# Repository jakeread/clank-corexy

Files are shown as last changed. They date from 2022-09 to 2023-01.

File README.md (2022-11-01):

## Clank-CoreXY

This is the CAD repo for the "minimal" variant of the [clank](https://clank.tools) machine platform: easily fabricated, multi-purpose cnc tools. Part of the [mtm project](mtm.cba.mit.edu) at the [MIT Center for Bits and Atoms](cba.mit.edu)

Read the [dev log](log/clank-corexy-log.md) for updates, and find the [most up to date CAD in /cad](cad). More documentation is at [clank.tools/build/corexy](https://clank.tools/build/corexy). 

This variant is `WIP WIP WIP`

## Controller Install

Firstly, I put the CAD and the Controller in the same repository, so it's a long clone. My bad.

### (1) Clone this repo (with Submodules!)

This repo uses submodules (at the time of writing) which are awesome for me but sometimes a pain in the ass. Updating git is awesome before you clone this repo, because newer git handles submodules much better. On linux, that means:

```
sudo apt-get update
sudo apt-get install git 
```

At the time of writing, that brought git up to `2.25.1` but it souldn't be too sensitive. 

Now you can clone this repo using 

```
git clone --recurse-submodules -j8 https://github.com/jakeread/clank-corexy.git`
```

The `-j8` is a performance speedup, allowing git to fetch up to 8 subs simultaneously. 

### (2) Install Node.js

Second, install node.js - I'm using v. `16.15.1` -> also fair-warning, installing node.js via `nvm` is the preferred strat.

### (3) Install with NPM

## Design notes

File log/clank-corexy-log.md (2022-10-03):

## 2022 08 07 

... there are more notes, in i.e. 2022-06? or -07?

I just want to figure sizes : sizes at the moment... 

| rail len | offsets | travel size |
| --- | --- | --- |
| 400mm X rail / bed | 50 + 42 + 107 = 199 | 201mm |
| 430mm Y rail | 100 + 2 | 328mm |
| 490mm Y bed | 

So given x, y travel sizes we have:

```
y rail size = y + 199
y bed size = y rail size 
x rail size = x + 102 
x bed size = x + 162 
```

alright then, I think I want ~ 250 x 300, this covers 8.5x11" letter and A4, it's all rough anyways, that means 

y rail, y bed = 450mm
x rail = 402mm (might as well 400mm)
x bed = 460mm 

alright alright, it'll be roughly square 

## 2022 08 20 

I had settled on a redesign of the toolchanger... I kind of think / hope that the 3rd rev is the winner, this is often the case in design anyways: 1st being hot garbage, 2nd taking the most time and refinement / teaching the most but ultimately not being quite it, then the 3rd embodying some big architectural changes that prevented the 2nd from really singing, and also the detail learnt through dev on the 2nd. Etc. So here we are.

Alright lol, clearly just mucking around today;

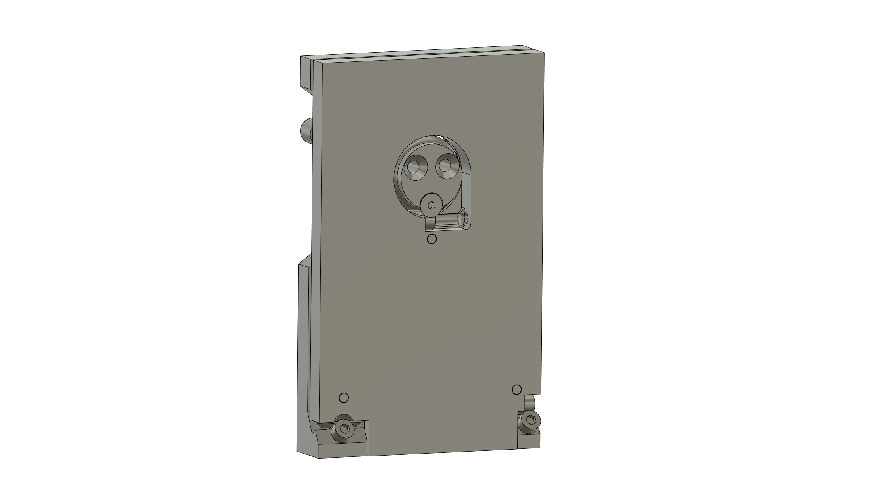
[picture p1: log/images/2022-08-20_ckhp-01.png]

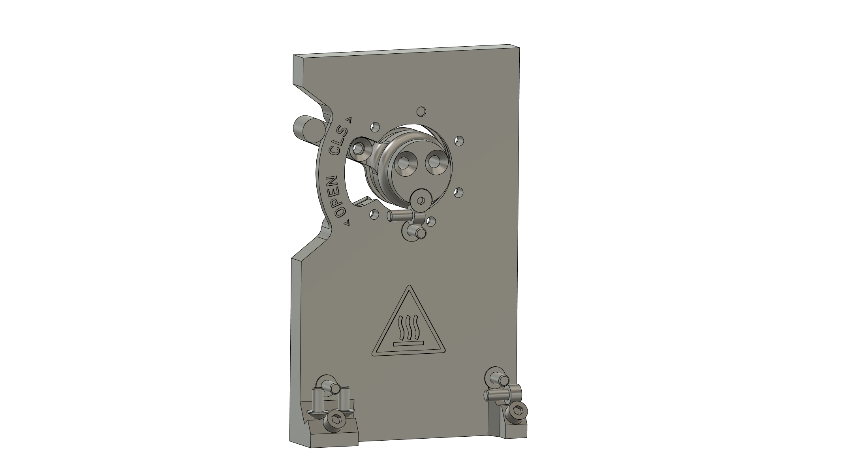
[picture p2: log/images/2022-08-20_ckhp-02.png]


The labels are fun... I figure that circuits would go *up top* with a very simple SHCS-head-into-tapered-entry-cylindrical-pocket across the pogo. Will fit widths for that eventually, time being I am going to hand operate this badboy, try to get clankite up-and-running and bed probing, etc. Things to design before auto-swapping with this:

- the z-axis, 
- the spindle, 
- the bed probe circuit (or friggen breadboard something homie) 
- then the PCB workflow, engraving bits use, etc... 

## 2022 08 21 

Some adjustments... 

- tighter, also wider lower left buttons
- don't crack open at the clamp-down M5 SHCS 
- taper on the key 

IDK about the XZ, it's for sure the crux of it. I think the Z driver should be perpendicular as it is in -stretch, maybe, and the toolchanger should get "gripped-around' i.e. have little rails on left and right sides that it travels along on, squanching it back into the face of the rail... not sure exactly, maybe it floats in front, but we are quickly ~ 40mm away from the rail, it's badness. 

## 2022 08 24

`2 * c_dist_manuel + 1.57 * ( pd_reduction + pd_pinion ) + ( ( pd_reduction - pd_pinion ) ^ 2 ) / ( 4 * c_dist_manuel )` 

OK... I keep on trying to tie this off with just an hour or two of work, it really wants a day for the CAD, to be solid enough for a motion system and honest application... things still remaining:

- z axis detail design:
  - another z-drive shift: hang the idlers out "the side" of the z-drive unit, lift the upper two carriages, attach the z-drive unit in close to the x-axis rollers, stick the pulleys through a hole up there...
  - lift the lower carriage elements, get at least +25mm lift,
  - belt details, tensioners, etc... 
  - ... maybe some detail for faster printing 
  - add a limit switch ffs 
- hotplate is the z axis body, etc, still hand-switched, time being though 
- add limits on XY 
- add x-gantry height to y-carriages mount 
- add stiffness on y-carriages-to-x-gantry 
- consider moving the motors to rearward, for classy packaging... ?
- ... a spindle, a bed probe ? 

... it actually might be the pro move to get a 100mm long linear rail, one carraige each, the long carriages, then we can absolutely sneak 'em in the back of the toolchanger, bigtime, i.e. there is 100mm of clear space in the back of this new beauty. Gives I think ~ 25mm of clearance on either side, which is good for most activities. Then squanch the carriages into a nice pocket in the x carriage, and we're in bigtime low-profile business, which will bring me some joy. 

https://www.amazon.com/100mm-Miniature-Bearing-Linear-Motion/dp/B07MR1S43Z/ 

That should come on Tuesday the 30th! And a print city! 

## 2022 08 30 

Well look at us, back here on time. I think I'm up to the Z axis. 

aye, alright, I've to head into lab now... but, done with the z, need limits all over the place and that toolplate adjustment, I might get back to it this evening but the aft. is for reading... 

- toolplate adjustments... bhcs angulars 
  - and lock this lever somehow, right ? servo implement? idk 
- left / right y situations 
- limits, limits, limits
  - motors back, before this ? 
- spindle coupling & 6-posn controller ? 

Doing limits now... then I *should* have some closure-lever-retainer, though *again* tempting to stick the servo in here, that'd solve both problems; having manual-operation available (?) is nice ? Indeed, I am a full hotplate-circuit away from this being auto, that's ~ a few days (at least) of design, fab, integration. 

OK, lol, I made this little clip... it's a crumpus;

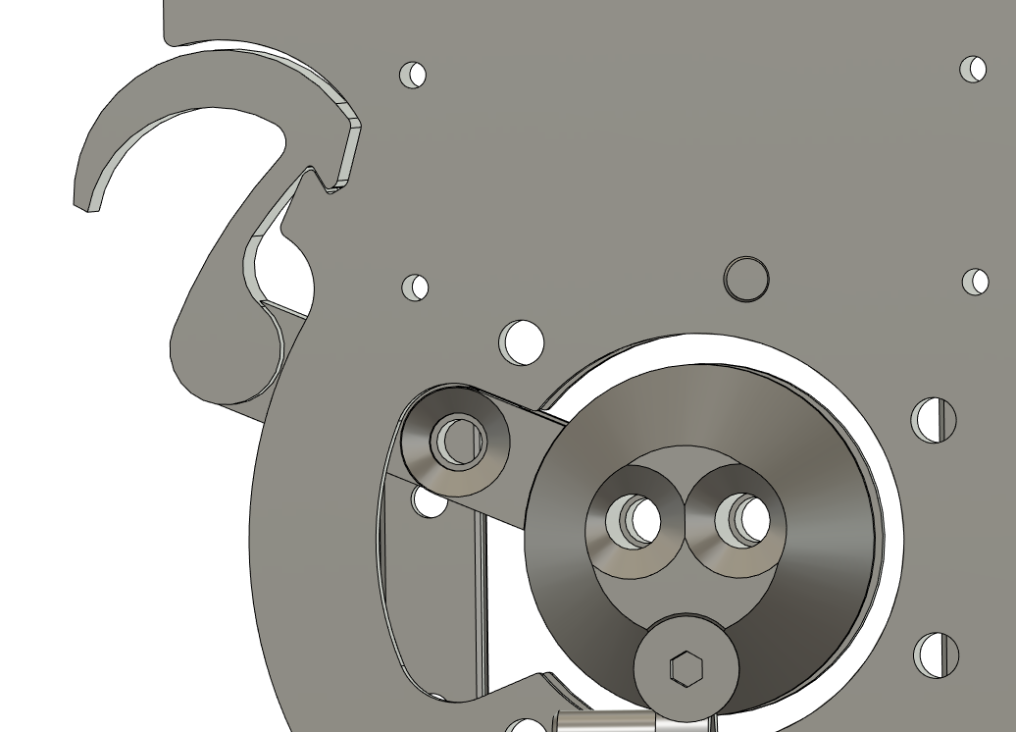
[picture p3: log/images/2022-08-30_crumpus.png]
crump


Then I want... last touches around XY: limits, maybe moving the motors back (?)...

OK,

- adjust YL...
- motors -> rear (?) 
- front pulley thing (?) 
- z motor gets the z limit
- one rear motor gets the home-to-rear, 
- one gets the home-to-left
- both use halt-broadcasts to run the limit cycle, limit system becomes graph configd, lol 

I think I need an idler map to do this properly, the corexy stuff. 

I think I can actually stack the rear two idlers, that'd be ideal. I'm going to work backwards... from front idler to rear motor... will probably tension up front. 

## 2022 08 31 

I've decided I think on belt geometry, so I need to figure how I'm going to tension things and mount up to the Y rails / bed. I had a thought much earlier about using the 3DP parts to pin the rails to the bed, and it might still be the trick... wanting also to leave one side float-ey. 

I think in the end, fastening extrusion to the bed w/ holes in the bed & M5 SHCS, then fastening elsewise to the extrusion is the most sensible: otherwise we are adding out-system fasteners i.e. wood screws etc. It's something of a shame, the bed being wonderfully stiff and available. 

... might have to add a 40mm M5 FHCS for idler mounting stuff... 

Adding limits on XY now, sheesh... 

Before sending to fab, I want to wash the CAD folder also, it's a mess in here. 

The X limit is trickier; it has to be oriented such that X can escape in Y... this next, then I think I'm done (?) in time for my planned 2pm-to-fab, not bad. 

OK I have limits, I think. Now this last adjustment on the tc plate, then I'm out to fab? 

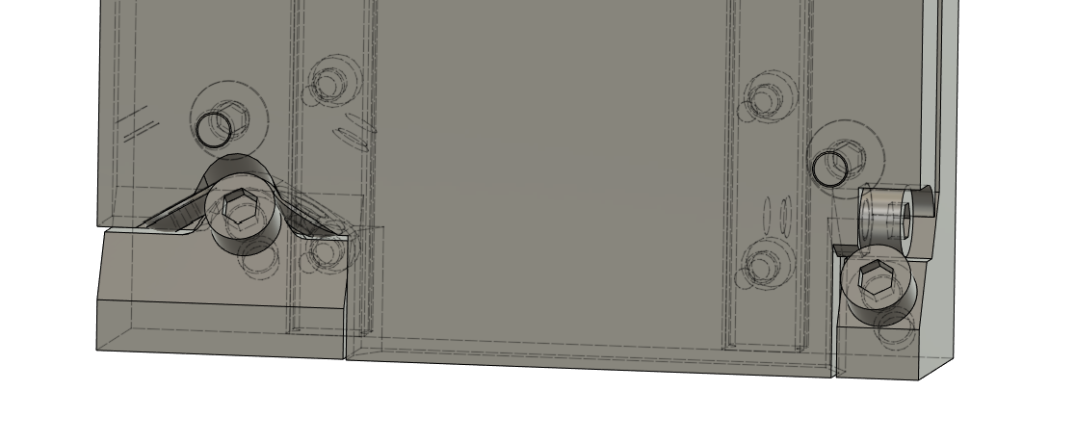
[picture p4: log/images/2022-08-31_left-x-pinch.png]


I believe that's going to be a lot better, my contact angles were ~ 20* center-to-side, now more like 45*... which would do more side-to-side work. Here's a comparison for posterity:

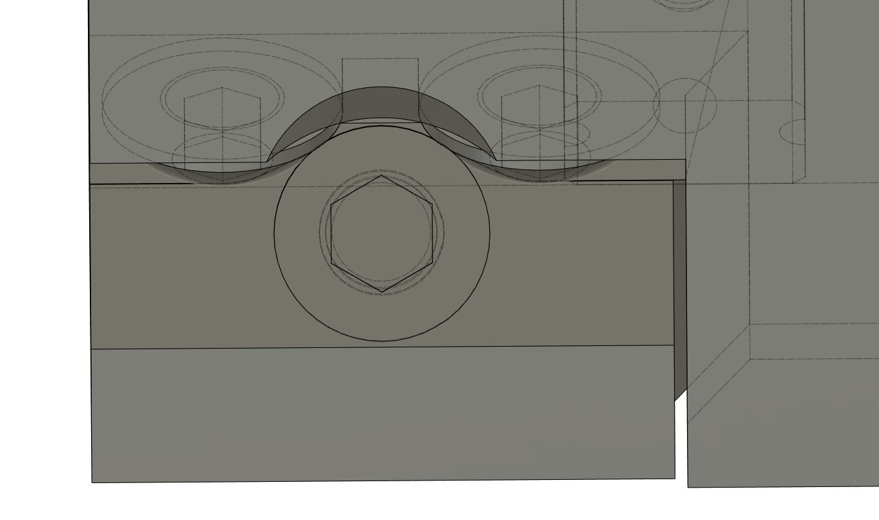
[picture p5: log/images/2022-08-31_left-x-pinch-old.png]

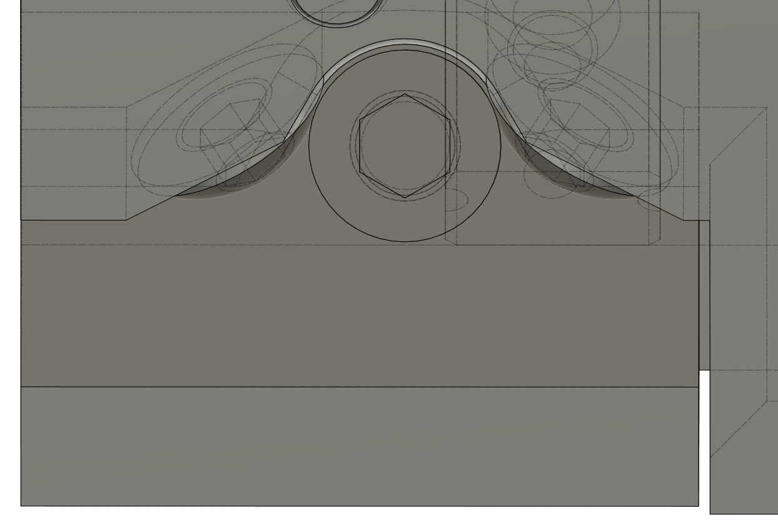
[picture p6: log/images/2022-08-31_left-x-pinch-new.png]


OK I'll print all of this, then next time we party it's going to be assembly, revisions (?) and controllers. 

- make fab 
- import new
- delete old... 

## 2022 09 01 

Sneaky assembly tonight. 

- the nose has ~ ? length M5 FHCS... should be 20, add 20 to set, more thread purchase 
- dial off ~ 0.15mm of "preload" at the toolchanger, preferrably on the tool side (!) of the CAD
- you *will need* assembly-order video for the XZ situation 
- remember to clean the cad up, yeah?
- M5x15 FHCS are prominent, not M5x14... 
- holes in the X face for Z linear rail bolt tightening 
- z drive thing... goes in w/ the only FHCS 15mm, erp, is that correct? 
- the z carriages could use, like, tapers ? for the install 
- overall, z real tough. sticky, I think just because of these missing tapers ? 
  - could do a z-roller printed in the side of the hotplate itself... simple groove, consider it, should be possible somehow, maybe there's a grooved part ?? 
  - can also just cut-out some of the hotplate 
- pulleys should get +1mm gap, for the rear stack's clearance: they're rubbing 
- motors don't move back bc shcs 
- you went *down* on the right side idler, not *up* - tf ? 
- idlers need much more tracking authority... consider using pulleys everywhere & 5mm SHCS shafts, or just get beefy with the print, 
- you should have parameters for M5 taps, thrus, chamfers, ibid M3s, and idler OD / inside teeth OD, outside teeth OD, flange OD ... 
- some screw-to-adjust-tension would be dreamy... esp. considering the balance. 
- all told this is probably one focussed day of CAD, maybe less, maybe the afternoon is + the spindle... 

oof, also can't even get the belts pinched on to the X carriage when this gd z-assembly is on, so I'm going to go looking briefly for what would be the life-saving z-crease part, it's probably just like, mini extrusion, or some channel. 

Ah yeah it's GD [this mfer](https://www.mcmaster.com/4630T117/) slipped in the sides of the toolchanger... there is also HFSQN4-1070, sneakier. 

GD, the cycles on this mfer. I can actually avoid them in this instance by just carving out some side-access for those belt clamps, then I can get on with controllers, front-end, etc. I'll do that for now. 

## 2022 09 05 

I've had handfuls of new ideas and I think I've decided that, while I'll probably leave this baby intact to dev the controller, I'll try to make the push through today for a kind of once-over on the device.

- starting w/ idler-improvement, and spec setting for belt heights-from-rails, idler diameters...
- tilted-rollers... dimension spec for cleaner drawings elsewhere, etc ? 
- clean for a new 'XZ' assembly, work out printed-in-place canti situations, etc 
  - this is the risky bit / why we leave the oldie together 
- split toolchanger and tool-body CAD? tool-body CAD should be easily communicable... 
- the z, the z, it's coupled into the toolchanger lever, etc etc, yikes 

OK, working through a list... 

I think this exercise was largely prompted by wanting to work out the XZ axis, but IDK if I can actually kick it as I'd hoped I would have... the trouble sort of mostly being that the XY belts arrive at the X carriage right around the same spot as the Z rollers want to. Then I would just be cycling back to making some QOL improvements / assemble-ability fixes. 

Yeah, the low-BOM tight z-axis is too tricky, maybe I'll prototype some new architectures later but for the time being I should carry on... 

Though I'm maybe dispairing too early... I'll give something a little go, see how it feels... 

And then I might split this day: half in this CAD, then to lab to send prints, afternoon setting up a controller (?) or designing the first tool... 

Year, this could maybe work? 

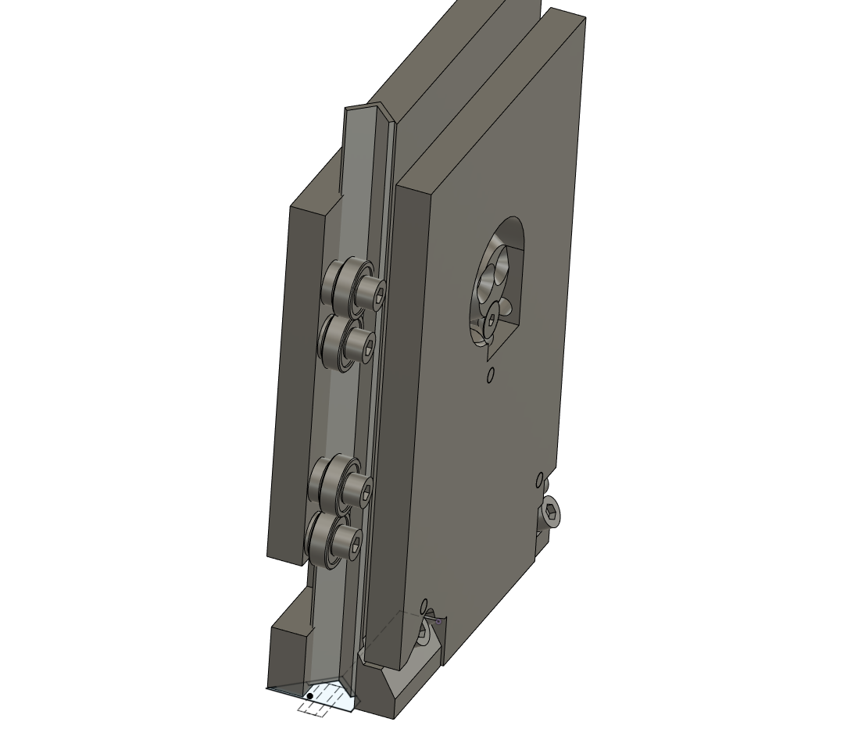
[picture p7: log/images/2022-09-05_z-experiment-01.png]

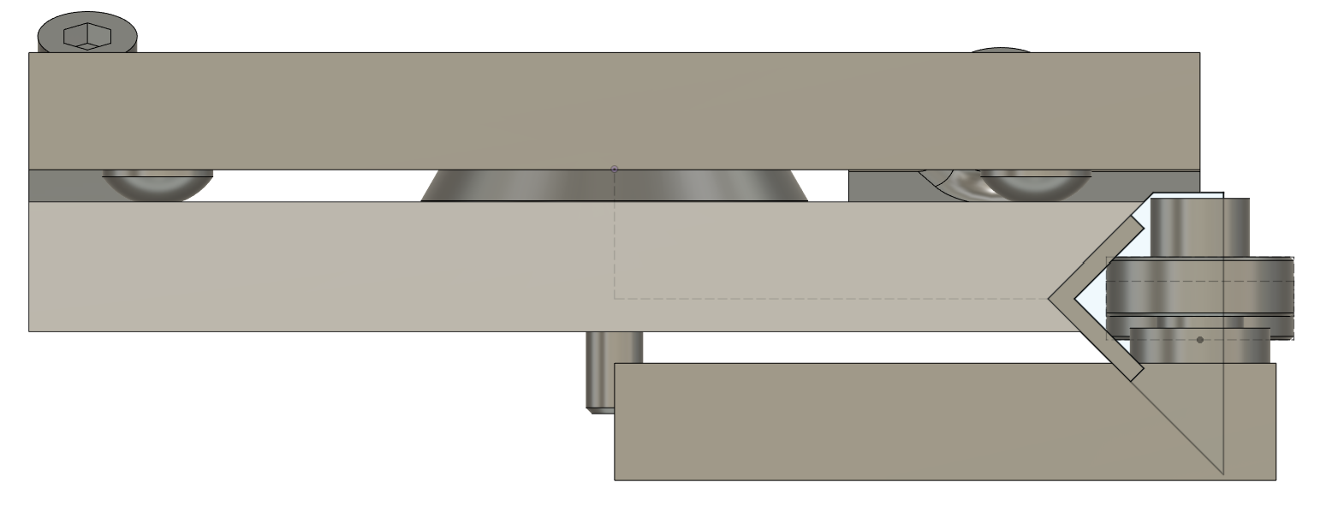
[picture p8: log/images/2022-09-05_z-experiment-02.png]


But I am going to leave off and get back to the other stuff: assembly-order issues, print-time tightening, screw annealing. Design needs to get done, this path is leading me down a few extra hours that are not available... will see if I can challenge someone else to make it work as well. 

The downside to this z axis is mostly that we can't take the Z off without taking the X axis off as well... that'll just be a welp. 

Alright, details even are enough for a day. I need still to work out the z body... 

Aye FFS, I think I'm nearly through it again?

Yeah... 830 then, might be, checking notes (?) then I'm into layout, printing, and a trip to the lab? 

### Notes Notes Notes 

OK, AFAIK I am through with this, again, now I need to check-check and then get plates onto printers... or, realistically, could do it tomorrow at lab (?) TBD. 

Checked the notes, and I believe I've done all the diffing. So, my week's goal is to wake up the controller for it / incl. XY transforms (maybe can do all ahead of the machine (?) - and stick a spindle on it, right? Whatever, I'll build this up, get it to home and move around, then see what the heart desires: might be toolchanger circuit, it might be fixed point motion, or touch probe circuits and PCB workflows, nobody knows. 

## 2022 09 08

I got one of these assembled today, now doing limits, controllers, etc.

I think probably one large-ish delta would be adding limit switch outputs on motor firmwares, and anyways getting those working w/ these powered switches, so that we can home the corexy. Also ofc the corexy transform, which afaik is simple (?). 

## 2022 09 14 

I'm spinning out CAD today, it seems like it would be worthwhile to also get the tool-plate dims... static? I.E. release a "version" of it - and make sure not to change it. 

The idler is kind of tough - some of the previous failed, at the top... understandably, the belt misalignment pulled 'em up and loaded the flanges. It's a thickness issue... really we want walls at ~ 2.5mm thick, which would carry an update through just about everywhere. I had it dialled for two-lines at 0.4mm nozzle... I'm going to just move right up to 2mm wall thickness for these, make 'em skookum, and will carry the adjustments through, it's a last chance to fux with these anyways. 

OK yikes, surprise hardware task:

- flow changes through z structure, (done)
- idler changes (out and update) (done)
- y carriage changes (done) 
- motor changes (shimmy and update) 
- check all flange clearances, everywhere, forever, and embiggen 
- you're done, ship to clank.tools 

Nearly done, ffs, this is an errand.

- just get plates out, enough to send to folks, you're in controller town still 

## 2022 09 20 

I'm going to setup some new plates to print today, and just adapt the tool changer to future-proof for circuits. 

My pogo pins have initial contact at 0.236" (6mm) from the pcb surface, and have 0.055" (1.4mm) of stroke, so I want the tool to be contacting at 5mm from the PCB surface... PCBs being 1.6mm thick, and I want 5mm final spacing (for 1mm of throw-s worth of pressure) I want the *bottom* of the toolchanger pcb to be... 5 + 1.6 * 2 = 8.2mm from the *back* of the tool. 

The existing gap is (allegedly) 2.75mm, so I need to push a 5.45 (5.5) millimeter pocket into the existing face. 

### "Deploying"

- should version the main assembly to a Fusion Version... that's "release" - ? and stash those are .f3z's ... 

## Kritical Dims

```
M5 "Tap" Hole           4.4 
M5 Thru Hole            5.5
M5 "Tap" Chamfer        0.5 
M5 FHCS Thru Chamfer    2.5 

Idler Physical OD       20.00
Idler PD Inside Teeth   22.10 
Idler PD Outside Teeth  20.70
Idler Total Height      12.5
Idler Clearance ID      14.5 

X Rail Face to Belt PL  6

Y Rail Top to Belt 1 CL 18.5
Y Rail Top to Belt 2 CL 32.5

Rail Edge to Roller CL  6.75
Roller Mount Hole Space 41
Roller Width            11.5
Roller Bearing Width    16
Roller Length           82
Roller Depth            20.5 (not centered!) 
```

### CAD Delta Desires 

- could rm M5x10 SHCS throughout and replace with FHCS, M5x14 SHCS, right? 
- check / sweep for a hardware BOM and tighten up overall if it seems possible 
- most important though is not getting bogged in the details, i.e. make a toolchanger circuit, make the head-board circuit, make the usb-bus python code, etc 

### Hardware Set

- BOM is on clank.tools 

### Docu-Notes

- the "extract BOM" fusion default script actually... is good enough for this application... 

### Dev Notes

- if we use long-throw limits (i.e. the trip-light type) we can whip into 'em at higher accels, shorten the homing cycle bigly 
- the final z-axis will likely use more bearing rollers and i.e. [this mfer](https://www.mcmaster.com/4630T117/) slipped in the sides of the toolchanger... there is also HFSQN4-1070, sneakier... will proceed with linear slides for now, I want to get up to controls, tools, etc. 

## Notes Notes

- it'd be wise / interesting to do the hertz contact model for the bearing-on-alu, and see under-what-loads we surpass a denting force... that would tell us if i.e. the MaaS machine needs to have substantially larger bearings, or, if this whole thing is a bad-bad idea: also the same model for delrin v-rollers, to compare 

### Hotplate Dev Notes

- put pogo above the rotary-key, use SHCS into cylindrical pockets w/ tapers for pogo coarse alignment; be simple... 

### Assy Notes

- it's possible to put one of these roller units together improperly, shouldn't be 
- try these roller units w/ just shoulder bolts for the MaaS Machine ? and triplet-style roller units... that can tip / shift for kinematics 
- assembly should just bolt straight onto some sheet, no back bar... opens some free space as well 
- base plate should be square if possible
- rather than making any holes / etc in plate, try 3DP corner bits ? then we are just rip-rip on the saw & blip blip into the sheet 
- would like to have the motors in the rear... seems possible (?) might be adding some rollers though... idk 
- lots of torsion-stiffness-loss thru these wimpy little y-carriage-to-x-beam-back-supports, they want that idler-stiffening top appendage... as do, I imagine, the rear studs 
- ya boi needs a Z axis, der... tempting to try clank hotplate, also tempting to either modify for low-BOM-count hotplate design *or* make a cut-er tool interface, but gd, do one, my guy

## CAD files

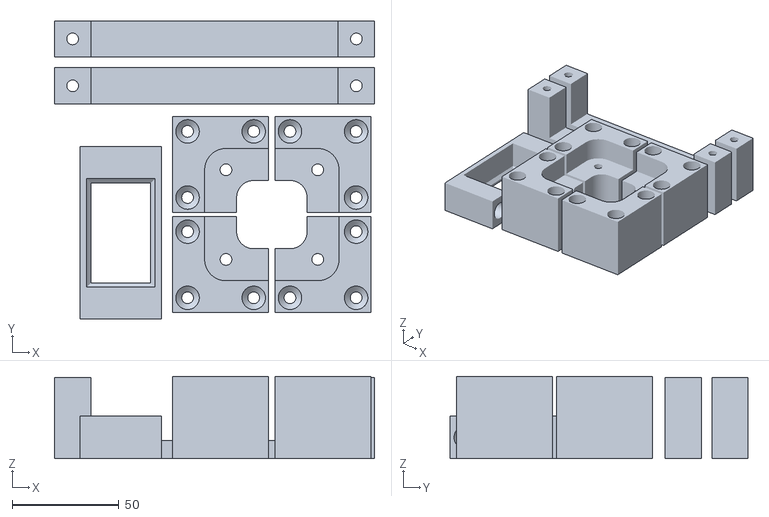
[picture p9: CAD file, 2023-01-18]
fab/clkxy-08-under-slings.stl
150.0 x 139.9 x 38.6

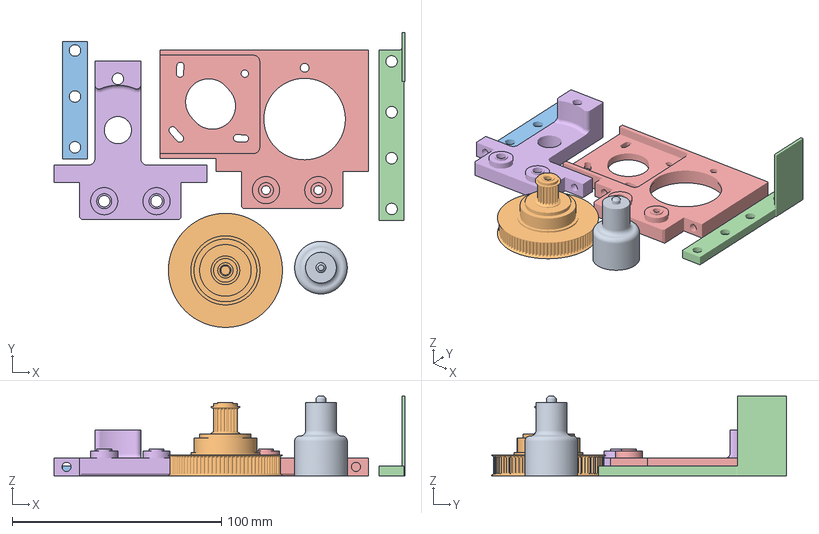
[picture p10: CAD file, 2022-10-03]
fab/prusa-mk3-06nozzle/clkxy-05-z.3mf
167.7 x 140.8 x 38.0 mm
clkxy-05-z.stl_1
clkxy-05-z.stl_2
clkxy-05-z.stl_3
clkxy-05-z.stl_4
clkxy-05-z.stl_5
clkxy-05-z.stl_6

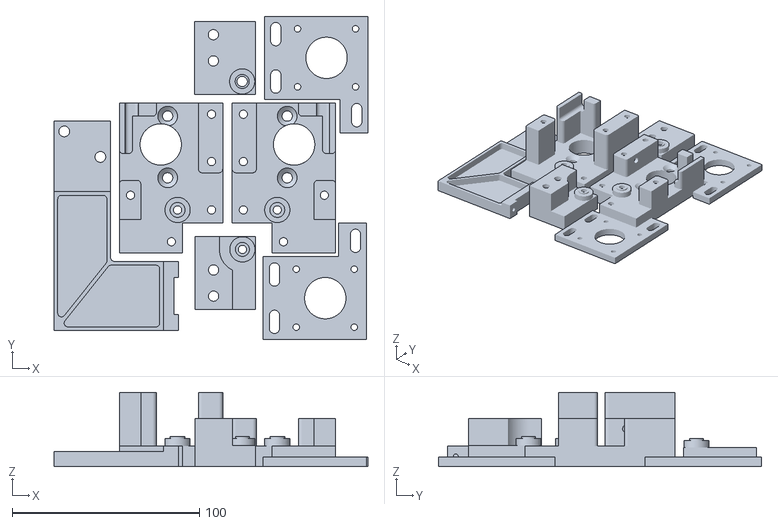
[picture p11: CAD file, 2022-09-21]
fab/clkxy-03-motors.stl
167.8 x 172.8 x 39.7

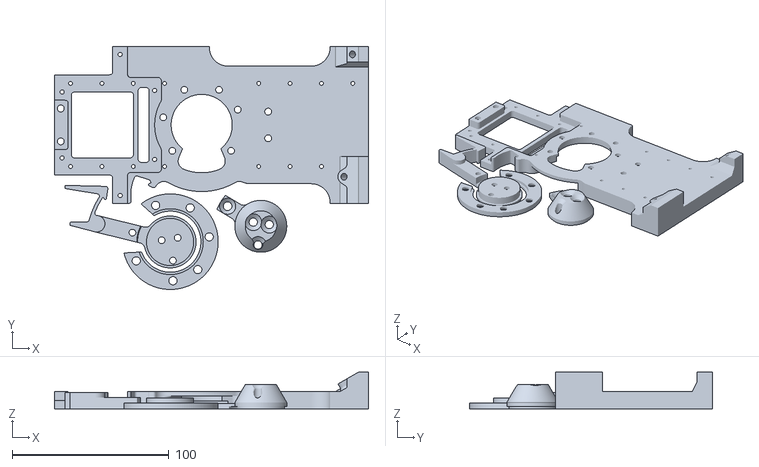
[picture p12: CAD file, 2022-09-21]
fab/clkxy-06-toolchanger.stl
200.2 x 154.9 x 23.5

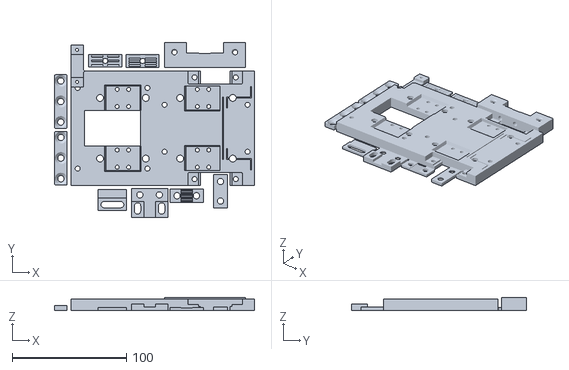
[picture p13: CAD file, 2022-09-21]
fab/clkxy-04-x.stl
174.8 x 152.7 x 11.0

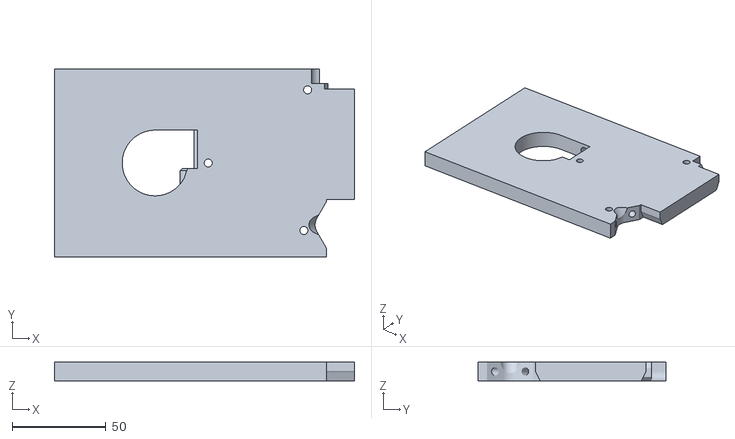
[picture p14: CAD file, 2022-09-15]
fab/clank-corexy-plate-07-tool-blank.stl
160.0 x 100.0 x 10.0

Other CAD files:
cad/sketches-etc/2022-07-06_clankite-v4.f3z
cad/sketches-etc/2022-09-05_xz-605-bearing-z-axis-trial.f3z

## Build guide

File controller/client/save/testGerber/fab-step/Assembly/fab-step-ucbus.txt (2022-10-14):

Partlist exported from C:/Dropbox/CBA/circuits/2020-11_fab-step/2021-06_fab-step-ucbus/fab-step-ucbus.sch at 6/19/2021 8:25 PM

Qty Value                   Device                  Package                   Parts           Description                                                                                                     PACKAGE PRECISION PROD_ID    TYPE VALUE VOLTAGE
1                           CONN_05X2SMD_LONGPADS   2X5-SHROUDED_SMD_LONGPADS J2              Multi connection point. Often used as Generic Header-pin footprint for 0.1 inch spaced/style header connections                                                
2   0.1uF                   CAP1206                 1206                      C5, C8          Capacitor                                                                                                       1206                                           
2   0R                      RESISTOR1206            1206                      R7, R11         Resistor                                                                                                        1206                                           
2   100mOhm                 RESISTOR1206            1206                      R1, R5          Resistor                                                                                                        1206                                           
2   10k                     RESISTOR1206            1206                      R2, R3          Resistor                                                                                                        1206                                           
3   10uF                    CAP1206                 1206                      C1, C3, C6      Capacitor                                                                                                       1206                                           
4   120R                    RESISTOR1206            1206                      R4, R6, R8, R9  Resistor                                                                                                        1206                                           
4   1uF                     CAP1206                 1206                      C2, C4, C7, C10 Capacitor                                                                                                       1206                                           
2   2-8X4-5_SWITCH          2-8X4-5_SWITCH          TACT-SWITCH-KMR6          S1, S2                                                                                                                                                                         
2   A4950FAB                A4950FAB                SOIC8_PAD_THRU_FAB        U2, U4                                                                                                                                                                         
1   ATSAMD21E18A-AFFAB      ATSAMD21E18A-AFFAB      TQFP-32-FAB               U1              The SAM D21 is a series of low-power microcontrollers using the 32-bit ARM®                                                                                    
1   JTAG                    CORTEX_JTAG_DEBUG_SMD   2X5-SMD-1.27MM            J1              Cortex Debug Connector - 10 pin                                                                                                   CONN-14503      JTAG         
2   LED                     LED                     LED1206                   U$1, U$2        LED                                                                                                                                                            
1   REGULATOR_SOT223        REGULATOR_SOT223        SOT223                    U3                                                                                                                                                                             
2   RS485-ISL83078EMSOP-FAB RS485-ISL83078EMSOP-FAB 8-MSOP-FAB                U5, U6                                                                                                                                                                         
1   USB_1/64                USB_1/64                DX4R005HJ5_64             X1              SMD micro USB connector as found in the fablab inventory.

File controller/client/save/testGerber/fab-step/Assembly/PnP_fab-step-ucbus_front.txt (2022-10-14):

C1	31.50	6.10	270.00	10uF	1206
C10	23.10	16.30	45.00	1uF	1206
C2	31.50	16.20	270.00	1uF	1206
C3	6.00	28.50	0.00	10uF	1206
C4	38.50	28.50	180.00	1uF	1206
C5	14.70	26.60	0.00	0.1uF	1206
C6	13.00	39.00	0.00	10uF	1206
C7	38.50	31.00	0.00	1uF	1206
C8	23.00	36.50	0.00	0.1uF	1206
J1	31.40	38.00	180.00	JTAG	2X5-SMD-1.27MM
J2	14.50	8.00	270.00		2X5-SHROUDED_SMD_LONGPADS
R1	5.00	20.00	0.00	100mOhm	1206
R11	31.50	11.00	90.00	0R	1206
R2	38.50	33.50	0.00	10k	1206
R3	33.50	32.50	180.00	10k	1206
R4	14.70	29.10	180.00	120R	1206
R5	10.00	33.00	270.00	100mOhm	1206
R6	23.00	39.00	180.00	120R	1206
R7	38.50	36.00	0.00	0R	1206
R8	26.00	4.00	270.00	120R	1206
R9	28.50	4.00	270.00	120R	1206
S1	38.20	25.60	180.00	2-8X4-5_SWITCH	TACT-SWITCH-KMR6
S2	32.00	23.30	270.00	2-8X4-5_SWITCH	TACT-SWITCH-KMR6
U$1	28.50	9.50	270.00	LED	LED1206
U$2	26.00	9.50	270.00	LED	LED1206
U1	24.50	26.00	270.00	ATSAMD21E18A-AFFAB	TQFP-32-FAB
U2	8.00	24.00	180.00	A4950FAB	SOIC8_PAD_THRU_FAB
U3	37.30	12.40	270.00	REGULATOR_SOT223	SOT223
U4	15.00	35.00	180.00	A4950FAB	SOIC8_PAD_THRU_FAB
U5	19.20	17.10	225.00	RS485-ISL83078EMSOP-FAB	8-MSOP-FAB
U6	15.60	18.90	225.00	RS485-ISL83078EMSOP-FAB	8-MSOP-FAB
X1	37.88	20.20	90.00	USB_1/64	DX4R005HJ5_64

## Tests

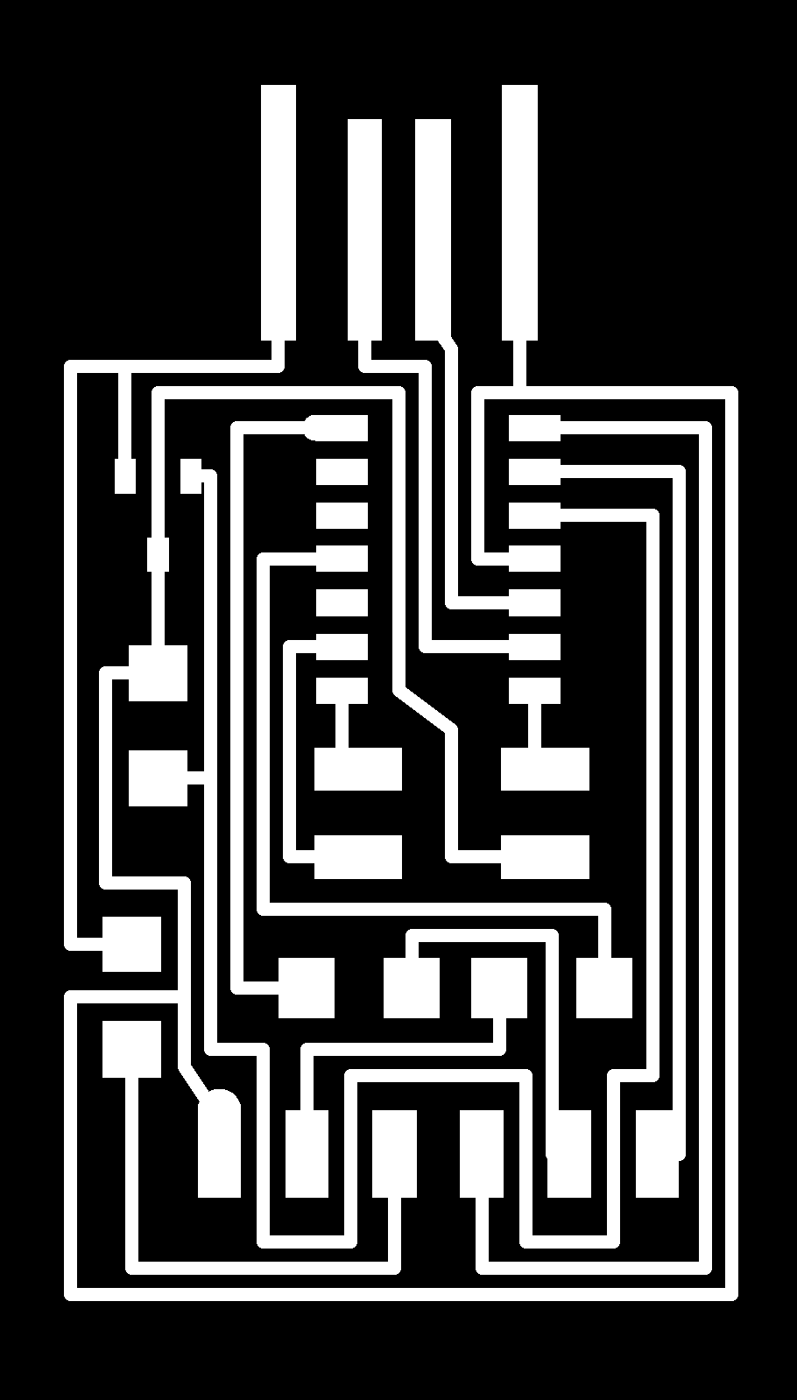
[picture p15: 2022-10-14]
controller/client/save/testPNG/hello.D11C.serial.5V.1.1.traces.png

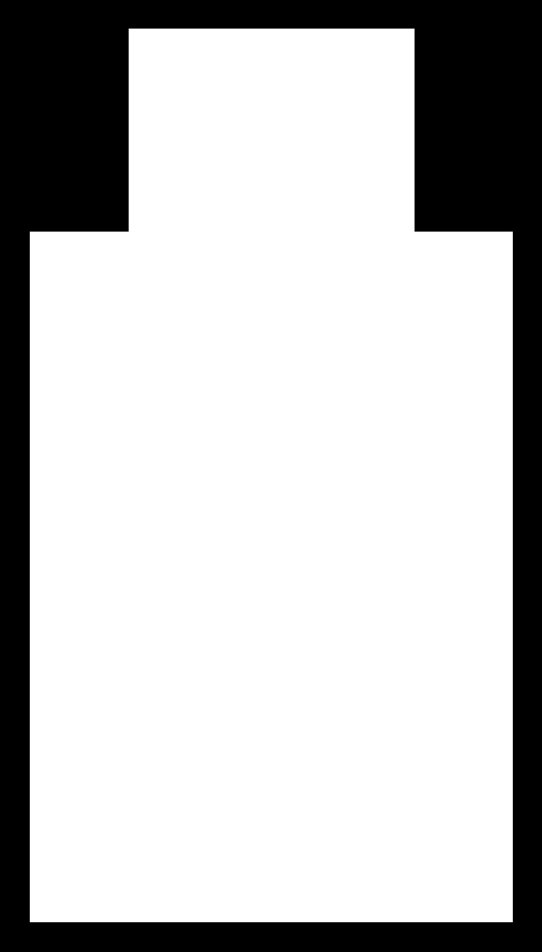
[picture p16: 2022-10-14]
controller/client/save/testPNG/hello.D11C.serial.5V.1.1.interior.png

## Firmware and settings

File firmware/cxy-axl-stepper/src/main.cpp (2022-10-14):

#include <Arduino.h>
#include "indicators.h"

#include "drivers/step_a4950.h"
#include "axl/axl.h"
#include "axl/axl_config.h"
#include "utils_samd51/clock_utils.h"

#include "osape/core/osap.h"
#include "osape/core/ts.h"
#include "osape/vertices/endpoint.h"
#include "osape_arduino/vp_arduinoSerial.h"
#include "osape_ucbus/vb_ucBusDrop.h"

OSAP osap("axl-stepper_z");
// OSAP osap("axl-stepper_rl");
// OSAP osap("axl-stepper_rr");

// -------------------------------------------------------- 0: USB Serial 

VPort_ArduinoSerial vpUSBSerial(&osap, "arduinoUSBSerial", &Serial);

// -------------------------------------------------------- 1: Bus Drop 

VBus_UCBusDrop vbUCBusDrop(&osap, "ucBusDrop"); 

// -------------------------------------------------------- 2: AXL Settings

EP_ONDATA_RESPONSES onAXLSettingsData(uint8_t* data, uint16_t len){
  // jd, then pairs of accel & vel limits,
  axlSettings_t settings;
  uint16_t rptr = 0;
  for(uint8_t a = 0; a < AXL_NUM_DOF; a ++){
    settings.accelLimits.axis[a] = ts_readFloat32(data, &rptr);
    settings.velocityLimits.axis[a] = ts_readFloat32(data, &rptr);
  }
  settings.queueStartDelayMS = ts_readUint32(data, &rptr);
  settings.ourActuatorID = ts_readUint8(data, &rptr);
  // ship em... 
  axl_setSettings(settings);
  // don't stash data, 
  return EP_ONDATA_ACCEPT;
}

Endpoint axlSettingsEP(&osap, "axlSettings", onAXLSettingsData);

// -------------------------------------------------------- 3: Axl Modal Requests 

EP_ONDATA_RESPONSES onStateData(uint8_t* data, uint16_t len){
  // check for partner-config badness, 
  if(len != AXL_NUM_DOF * 4 + 2){ OSAP::error("state req has bad DOF count"); return EP_ONDATA_REJECT; }
  // we have accel, rate, posn data, 
  vect_t targ;
  uint16_t rptr = 0;
  uint8_t mode = data[rptr ++];
  uint8_t set = data[rptr ++];
  for(uint8_t a = 0; a < AXL_NUM_DOF; a ++){
    targ.axis[a] = ts_readFloat32(data, &rptr);
  }
  // set or target?
  if(set){
    switch(mode){
      case AXL_MODE_POSITION:
        if(axl_isMoving()){
          OSAP::error("AXL can't set pos while moving");
          break;
        }
        axl_setPosition(targ);
        break;
      default:
        OSAP::error("we can only 'set' position, others are targs");
        break;
    }
  } else {
    switch(mode){
      // case AXL_MODE_ACCEL:
      //   // axl_setAccelTarget(targ);
      //   break;
      case AXL_MODE_VELOCITY:
        axl_setVelocityTarget(targ);
        break;
      case AXL_MODE_POSITION:
        axl_setPositionTarget(targ);
        break;
      default:
        OSAP::error("AXL state targ has bad / unrecognized mode " + String(mode));
        break;
    }
  }
  // since we routinely update it w/ actual states (not requests) 
  return EP_ONDATA_REJECT;
}

uint8_t stateDataDummy[256];

boolean beforeAxlStateQuery(void);

Endpoint stateEP(&osap, "axlState", onStateData, beforeAxlStateQuery);

boolean beforeAxlStateQuery(void){
  uint16_t len = axl_getState(stateDataDummy);
  stateEP.write(stateDataDummy, len);
  return true;
}

// -------------------------------------------------------- 4: Axl Queue Addition 

EP_ONDATA_RESPONSES onSegmentData(uint8_t* data, uint16_t len){
  // careful, if you add a new field in axlPlannedSegment_t, recall you have to copy 
  // it manually into the buffer (!) 
  axlPlannedSegment_t segment;
  uint16_t rptr = 0;
  // location of segment-in-sequence, to count continuity, 
  segment.segmentNumber = ts_readUint32(data, &rptr);
  // which actuator is requested to ack this mfer, 
  segment.returnActuator = ts_readUint8(data, &rptr);
  // is it the end of this stream ?
  segment.isLastSegment = ts_readBoolean(data, &rptr);
  OSAP::debug("segnum, isLast " + String(segment.segmentNumber) + ", " + String(segment.isLastSegment));
  // unit vector describing segment's direction, 
  for(uint8_t a = 0; a < AXL_NUM_DOF; a ++){
    segment.unitVector.axis[a] = ts_readFloat32(data, &rptr);
  }
  // start vel, accel-rate (up, and down), max velocity, final velocity, distance (all +ve)
  segment.vi = ts_readFloat32(data, &rptr);
  segment.accel = ts_readFloat32(data, &rptr);
  segment.vmax = ts_readFloat32(data, &rptr);
  segment.vf = ts_readFloat32(data, &rptr);
  segment.distance = ts_readFloat32(data, &rptr);
  // and send it... 
  axl_addSegmentToQueue(segment);
  // don't write to endpoint... 
  return EP_ONDATA_REJECT;
}

Endpoint precalculatedSegmentEP(&osap, "segmentsIn", onSegmentData);

// -------------------------------------------------------- 5: Halt Input 

EP_ONDATA_RESPONSES onHaltInData(uint8_t* data, uint16_t len){
  axl_halt(data[0]);
  return EP_ONDATA_REJECT;
}

Endpoint haltInEP(&osap, "haltIn", onHaltInData);

// -------------------------------------------------------- 6, 7, 8: Outputs

Endpoint haltOutEP(&osap, "haltOut");
Endpoint segmentAckOutEP(&osap, "segmentAckOut");
Endpoint segmentCompleteOutEP(&osap, "segmentCompleteOut");

// -------------------------------------------------------- 9: Motor Settings

uint8_t axisPick = 0;
boolean invert = false; 
uint16_t microstep = 4; 
float spu = 100.0F;
float cscale = 0.1F;

// aye, there should be a void onData overload... less confusing 
EP_ONDATA_RESPONSES onMotorSettingsData(uint8_t* data, uint16_t len){
  uint16_t rptr = 0;
  axisPick = data[rptr ++];
  ts_readBoolean(&invert, data, &rptr);
  ts_readUint16(&microstep, data, &rptr);
  spu = ts_readFloat32(data, &rptr);
  cscale = ts_readFloat32(data, &rptr);
  stepper_hw->setMicrostep(microstep);
  stepper_hw->setCurrent(cscale);
  stepper_hw->setInversion(invert);
  return EP_ONDATA_ACCEPT;
}

Endpoint motorSettingsEP(&osap, "motorSettings", onMotorSettingsData);

// -------------------------------------------------------- 10: Limit Halt-Output:

Endpoint limitHaltEP(&osap, "limitSwitchState");

#define LIMIT_PIN 23
#define LIMIT_PORT 0 

void limitSetup(void){
  PORT->Group[LIMIT_PORT].DIRCLR.reg = (1 << LIMIT_PIN);
  PORT->Group[LIMIT_PORT].PINCFG[LIMIT_PIN].bit.INEN = 1;
  // pullup 
  PORT->Group[LIMIT_PORT].OUTSET.reg = (1 << LIMIT_PIN);
}

boolean checkLimit(void){
  return (PORT->Group[LIMIT_PORT].IN.reg & (1 << LIMIT_PIN));
}

// -------------------------------------------------------- 11: Motion State 

boolean beforeMotionStateQuery(void);

Endpoint motionStateEP(&osap, "motionState", beforeMotionStateQuery);

uint8_t dummyMotionStateData[1];

boolean beforeMotionStateQuery(void){
  if(axl_isMoving()){
    dummyMotionStateData[0] = 1;
  } else {
    dummyMotionStateData[0] = 0;
  }
  motionStateEP.write(dummyMotionStateData, 1);
  return true;
}

// -------------------------------------------------------- Arduino Setup 

void setup() {
  CLKLIGHT_SETUP;
  ERRLIGHT_SETUP;
  DEBUG1PIN_SETUP;
  DEBUG2PIN_SETUP;
  // port begin 
  vpUSBSerial.begin();
  vbUCBusDrop.begin();
  // setup stepper machine 
  stepper_hw->init(false, 0.0F);
  stepper_hw->setMicrostep(4);
  // setup controller
  axl_setup();
  // setup limit swootch
  limitSetup();
  // ticker begin:
  // d51ClockUtils->start_ticker_a(AXL_TICKER_INTERVAL_US);
}

// -------------------------------------------------------- Das Loop 

uint32_t lastBlink = 0;
uint32_t blinkInterval = 50; // ms 

uint8_t axlData[256];
uint16_t axlDataLen = 0;

uint32_t lastLimitCheck = 0;
uint32_t limitCheckInterval = 1; // ms, helps to debounce, bummer to be running this often 
uint8_t limitTrace = 0; // 8-wide 1-bit state trace... for edge-masking, 
boolean limitState = false;
uint8_t dummy[2] = { 0, 0 }; // lol, typed endpoints wanted ! 

void loop() {
  osap.loop();
  // check for halt info... 
  axlDataLen = axl_getHaltPacket(axlData);
  if(axlDataLen){
    haltOutEP.write(axlData, axlDataLen);
  }
  // check for queueAck info... 
  axlDataLen = axl_getSegmentAckMsg(axlData);
  if(axlDataLen){
    segmentAckOutEP.write(axlData, axlDataLen);
  }
  // check for queueSegmentComplete 
  axlDataLen = axl_getSegmentCompleteMsg(axlData);
  if(axlDataLen){
    segmentCompleteOutEP.write(axlData, axlDataLen);
  }
  // refresh stepper hw, 
  stepper_hw->dacRefresh();
  if(lastBlink + blinkInterval < millis()){
    lastBlink = millis();
    CLKLIGHT_TOGGLE;
    // updateStatesEP();
    //axl_printHomeState();
  }
  // this, i.e, could be on an endpoint's loop code, non?
  if(lastLimitCheck + limitCheckInterval < millis()){
    lastLimitCheck = millis();
    // shift left one & tack bit on the end, 
    limitTrace = limitTrace << 1;
    limitTrace |= checkLimit() ? 1 : 0;
    // swap on positive or -ve edges, 
    if(limitTrace == 0b11111111 && limitState == false){
      ERRLIGHT_ON;
      limitState = true;
      dummy[0] = 1;
      limitHaltEP.write(dummy, 1);
    } else if (limitTrace == 0b00000000 && limitState == true){
      ERRLIGHT_OFF;
      limitState = false;
      dummy[0] = 0;
      limitHaltEP.write(dummy, 1);
    }
  }
  // if(errLightOn && errLightOnTime + 250 < millis()){
  //   ERRLIGHT_OFF;
  //   errLightOn = false;
  // }
}

// -------------------------------------------------------- Small-Time Ops 

volatile float stepRatchet = 0.0F;
void axl_onPositionDelta(uint8_t axis, float delta, float absolute){
  if(axis != axisPick) return;
  stepRatchet += delta * spu;
  if(stepRatchet >= 1.0F){
    stepper_hw->dir(true);
    stepper_hw->step();
    stepRatchet -= 1.0F;
  } else if (stepRatchet <= -1.0F){
    stepper_hw->dir(false);
    stepper_hw->step();
    stepRatchet += 1.0F;
  }
}

// void TC0_Handler(void){
//   DEBUG1PIN_ON;
//   TC0->COUNT32.INTFLAG.bit.MC0 = 1;
//   TC0->COUNT32.INTFLAG.bit.MC1 = 1;
//   // run the loop, 
//   axl_integrator();
//   DEBUG1PIN_OFF;
// }

void ucBusDrop_onRxISR(void){
  DEBUG1PIN_ON;
  axl_integrator();
  DEBUG1PIN_OFF;
}

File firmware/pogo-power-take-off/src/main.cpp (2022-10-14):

#include <Arduino.h>

#include "indicators.h"
#include "utils_samd51/clock_utils.h"

#include "osape/core/osap.h"
#include "osape/vertices/endpoint.h"

#include "osape_arduino/vp_arduinoSerial.h"

#include "osape_ucbus/vb_ucBusHead.h"

// -------------------------------------------------------- OSAP ENDPOINTS SETUP

OSAP osap("motion-head");

VPort_ArduinoSerial vpUSBSer(&osap, "arduinoUSBSerial", &Serial);   // 0

VBus_UCBusHead vbUCBusHead(&osap, "ucBusHead");                     // 1

// -------------------------------------------------------- POWER MODES 

// 5v bus hi-side sw on PB23
#define SW_5V_BUS_ON PIN_HI(1, 23)
#define SW_5V_BUS_OFF PIN_LO(1, 23)
#define SW_5V_BUS_SETUP PIN_SETUP_OUTPUT(1, 23); PIN_LO(1, 23)

#define SW_24V_BUS_ON PIN_HI(1, 14)
#define SW_24V_BUS_OFF PIN_LO(1, 14)
#define SW_24V_BUS_SETUP PIN_SETUP_OUTPUT(1, 14); PIN_LO(1, 14)

#define SW_5V_POGO_ON PIN_HI(1, 22)
#define SW_5V_POGO_OFF PIN_LO(1, 22)
#define SW_5V_POGO_SETUP PIN_SETUP_OUTPUT(1, 22); PIN_LO(1, 22)

#define SW_24V_POGO_ON PIN_HI(1, 17)
#define SW_24V_POGO_OFF PIN_LO(1, 17)
#define SW_24V_POGO_SETUP PIN_SETUP_OUTPUT(1, 17); PIN_LO(1, 17)

// we'll use this to write to the endpoint... 
void publishPowerStates(boolean stBus5V, boolean stBus24V, boolean stPogo5V, boolean stPogo24V);

// make changes 
void powerStateUpdate(boolean stBus5V, boolean stBus24V, boolean stPogo5V, boolean stPogo24V){
  // guard against bad states, 
  if(stBus24V && !stBus5V) stBus24V = false;
  if(stPogo24V && !stPogo5V) stPogo24V = false;
  // if either 24v needs to turn off, do that now: 
  if(!stBus24V) SW_24V_BUS_OFF;
  if(!stPogo24V) SW_24V_POGO_OFF;
  // a delay for charges to bleed... maybe unneccessary, or better done with a proper async wait 
  delay(50);
  // set 5v next in either dir, 
  stBus5V ? SW_5V_BUS_ON : SW_5V_BUS_OFF;
  stPogo5V ? SW_5V_POGO_ON : SW_5V_POGO_OFF;
  // and 24v powering up, 
  if(stBus24V) SW_24V_BUS_ON;
  if(stPogo24V) SW_24V_POGO_ON;
  // now ... would like to write to the endpoint 
  publishPowerStates(stBus5V, stBus24V, stPogo5V, stPogo24V);
}

EP_ONDATA_RESPONSES onPowerData(uint8_t* data, uint16_t len){
  // read requested states out 
  boolean stBus5V, stBus24V, stPogo5V, stPogo24V;
  uint16_t rptr = 0;
  ts_readBoolean(&stBus5V, data, &rptr);
  ts_readBoolean(&stBus24V, data, &rptr);
  ts_readBoolean(&stPogo5V, data, &rptr);
  ts_readBoolean(&stPogo24V, data, &rptr);
  // run the update against our statemachine 
  powerStateUpdate(stBus5V, stBus24V, stPogo5V, stPogo24V);
  // here's a case where we'll never want to let senders to 
  // update our internal state, so we just return 
  return EP_ONDATA_REJECT;
  // this means that the endpoint's data store will remain unchanged (from the write) 
  // but remains true to what was written in when we updated w/ the powerStateUpdate fn... 
}

Endpoint powerEp(&osap, "powerSwitches", onPowerData);      // 6: Power Switches 

void publishPowerStates(boolean stBus5V, boolean stBus24V, boolean stPogo5V, boolean stPogo24V){
  uint8_t powerData[4];
  uint16_t wptr = 0;
  ts_writeBoolean(stBus5V, powerData, &wptr);
  ts_writeBoolean(stBus24V, powerData, &wptr);
  ts_writeBoolean(stPogo5V, powerData, &wptr);
  ts_writeBoolean(stPogo24V, powerData, &wptr);
  powerEp.write(powerData, wptr);
}

// -------------------------------------------------------- 8: Precalcd-move-adder / producer 

// Endpoint precalculatedMoveEP(&osap, "precalculatedMoveOutput");

// -------------------------------------------------------- SETUP 

void setup() {
  ERRLIGHT_SETUP;
  CLKLIGHT_SETUP;
  DEBUG1PIN_SETUP;
  DEBUG2PIN_SETUP;
  DEBUG3PIN_SETUP;
  DEBUG4PIN_SETUP;
  // setup the power stuff 
  SW_5V_BUS_SETUP;
  SW_24V_BUS_SETUP;
  SW_5V_POGO_SETUP;
  SW_24V_POGO_SETUP;
  // write states, all off until told otherwise, 
  powerStateUpdate(false, false, false, false);
  // osap
  vpUSBSer.begin();
  vbUCBusHead.begin();
  // startup axl, 
  // axl_setup(); 
  // bus runs on 10kHz ticker 
  d51ClockUtils->start_ticker_a(1000000/10000); 
  // turn 5v on by default,  
  powerStateUpdate(false, false, false, false);
}

unsigned long epUpdateInterval = 250; // ms 
unsigned long lastUpdate = 0;
uint16_t moveDataLen = 0;
uint8_t moveBuffer[128];

void loop() {
  // main recursive osap loop:
  osap.loop();
} // end loop 

// runs on period defined by timer_a setup: 
volatile uint32_t timeTick = 0;
volatile uint64_t timeBlink = 0;

void TC0_Handler(void){
  // runs at period established above... 
  TC0->COUNT32.INTFLAG.bit.MC0 = 1;
  TC0->COUNT32.INTFLAG.bit.MC1 = 1;
  // do bus action first: want downstream clocks to be deterministic-ish
  vbUCBusHead.timerISR();
  // do blinking, lol
  timeBlink ++;
  if(timeBlink > 500){
    DEBUG1PIN_TOGGLE;
    timeBlink = 0; 
  }
}

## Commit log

2022-09-15 hello formerly known as clankite
    [2022-07-06_clankite-v4.f3z, 2022-09-05_xz-605-bearing-z-axis-trial.f3z]
2022-09-15 add fab plates, update cad
    [clank-corexy-plate-04.stl, clank-corexy-plate-05.stl, clank-corexy-plate-06.stl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]
2022-09-20 update plates for toolblank mount holes and tool changer circuit mounts
    [clank-corexy-plate-06.stl]
2022-09-20 correct some minor CAD errors
    [clank-corexy-plate-05.stl]
2022-09-21 improve plate grouping
    [clank-corexy-plate-04.stl, clank-corexy-plate-05.stl, clank-corexy-plate-06.stl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]
2022-09-21 update plates again
    [clkxy-03-motors.stl]
2022-09-21 add prusa gcodes
    [clkxy-03-motors.stl]
2022-10-03 update a toolchanger cad for hotplate pogo power take off, add 775 spindle mount
    [clkxy-05-z.3mf, clkxy-08-775-mount.stl]
2022-10-03 one more, add magnet lever-sense to tc
2022-10-14 stepper fw branch here
2022-10-14 track js controller, swap to corexy in osapjs sub
    [copper_bottom.gbr, copper_top.gbr, drill_1_16.xln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]
2022-10-14 hello world controller, some plate updates
2022-10-15 some wiring bits to fab
    [clkxy-08-775-mount.stl, clkxy-08-under-slings.stl]
2022-10-15 halfway through working out the traces-outline offset bug
2022-10-20 controller upd8s, fba upd8s
    [clkxy-08-under-slings.stl]
2022-11-30 clank-corexy fab / cad up to date with the new hotness
    [2022-07-06_clankite-v4.f3z, 2022-09-05_xz-605-bearing-z-axis-trial.f3z]
2023-01-18 circuit agnostic toolchanger, stronger rubber feet
    [clkxy-08-under-slings.stl]
